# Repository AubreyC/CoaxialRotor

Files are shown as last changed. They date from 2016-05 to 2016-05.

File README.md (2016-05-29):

Coaxial-Rotor instructions
==========================

This document presents the main steps to build a flyable coaxial-rotor UAV. 

## Manufactering process
	
The Coaxial-rotor UAV is composed of off-the-shelf electronic parts and plywood / foam-board laser cut parts. The following list of components and CAD files corresponds to a medium-size configuration shown in the following picture. 

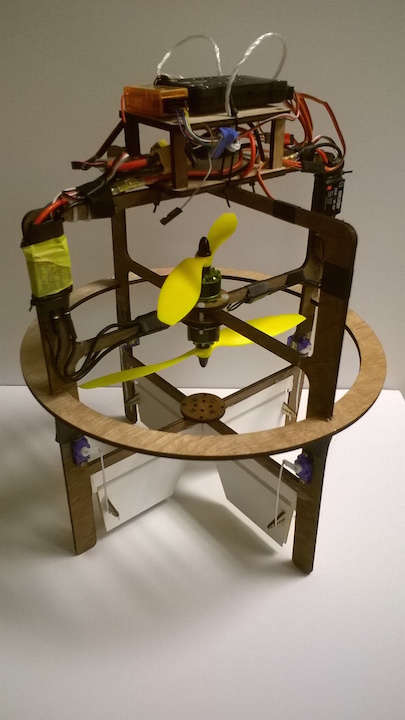
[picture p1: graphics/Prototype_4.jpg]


Assembled Prototype

### Off the shelf

- PIXHAWK Hardware Autopilot 
- RC receiver: OrangeRx R615X
- Battery : XXX
- ESC (with BEC): 2 x Mystery 30A M-30 with BEC 5V
- Motors: 2 x Multistar 2209-1200 
- Propellers: 2 x 
- 4 servomotors: 4 x Hextronik HXT 500

### Manufactering:
##### Material needed  
- Plywood (6mmm and 3mm)
- Foam-board (6mm)
- Laser-cut machine 
- Hot glue 
- Zip-ties

##### CAD files

This Coaxial-rotor UAV has been designed to be fully laser-cut, and assembled using hot-glue and zip-ties. The CAD files are in the [CAD folder](https://github.com/AubreyC/CoaxialRotor/tree/master/CAD). 

###### Plywood 5mm:
- Main Frame: Part 1 (frame_1.SLDPRT) / Part 2 (frame_2.SLDPRT)
- Motor mount: 2 x Part (motorMount.SLDPRT)
- Autopilot Plate: 2 x Part (plate.SLDPRT)
- Column plate: 4 x (columnPlate_long.SLDPRT / columnPlate_short.SLDPRT)

###### Plywood 2.5mm:

- Hinge: 4 x Part (hinge.SLDPRT)

######  Foam-board (6mm):
- Control surfaces: Part 1 (controlSurface_1_v2.SLDPRT) / Part 2 (controlSurface_2_v2.SLDPRT) 
	
__NOTE:__ On the control surface, the second line needs to be scored (and not cut), in order to create a hinge with the foam-board.

##### Laser-cut settings (Epilog Legend 36 EXT)

| Foam-board | Speed | Power  | Frequency |
| --- |:---:| :----: |:---:|
| Scoring | 90		 | 100 | 5000		 |		
| Cutting | 40 	 | 100 | 5000		 |

| Plywood 	| Speed | Power  | Frequency |
| ---|:---:| :----: |:---:|
| Cutting (3mm) | 25		 | 	100  | 500	 |		
| Cutting (6mm) | 8  	 | 100  | 500 	 |

## Code base:

For the flight control, the [PX4 flight stack](http://px4.io/) is used for its modularity and clarity as flight control software. 

The devlopment is done under linux [Ubuntu 14.04 LTS](http://releases.ubuntu.com/14.04/). The easiest way to get started is to build a virtual machine using [VirtualBox](https://help.ubuntu.com/community/VirtualBox). 

The PX4 development toolchain needs to be installed. Please follow the instructions: [PX4 flight stack - Installing toolchain](http://dev.px4.io/starting-installing-linux.html).

A lots of additional information can be found in the [PX4 flight stack - Development Guide](http://dev.px4.io). 

### Coaxial-rotor controller

Using the PX4 flight stack allows to re-use most of the code base, and to adapt it for this configuration. 

The coaxial-rotor uses the same controller as a quadcopter, and re-map the output of the controller (forces and torques to apply to the system) to the actuators. The mapping from the output of the attitude controller to the actuators is called the [PX4 flight stack - Mixer](http://dev.px4.io/concept-mixing.html).

For the Coaxial-rotor design, the mixer is designed as shown in the following figure: 

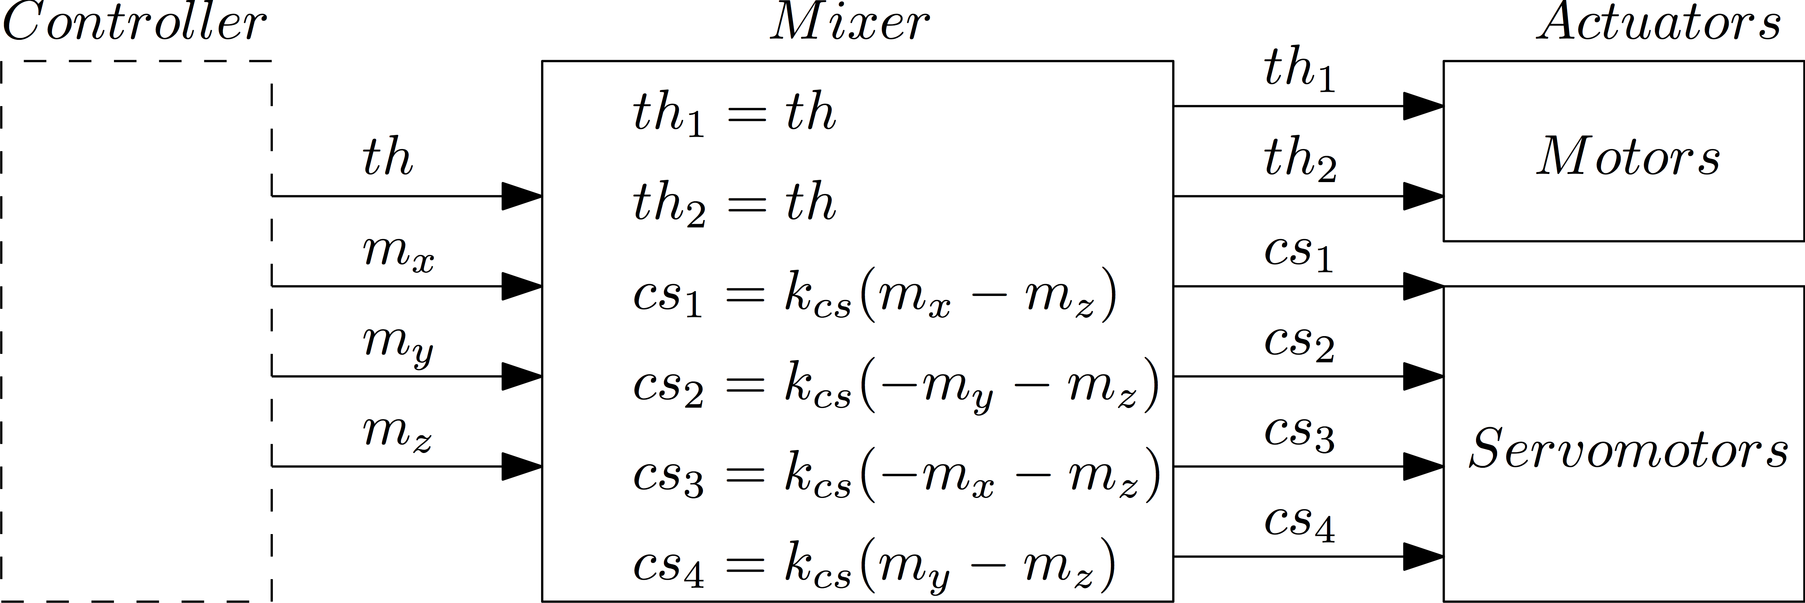
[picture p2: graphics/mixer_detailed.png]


#### Modifications
 
To support this configuration, the following modifications have been made to the base code: 
- __New Start up script__: Start the appropriate modules for this configuration [Start up - Coaxial-rotor](https://github.com/AubreyC/Firmware/blob/coaxial_rotor/ROMFS/px4fmu_common/init.d/15002_coax_rotor)
- __New Mixer__: Map the output of the attitude controller to the actuators. [Mixer - Coaxial-rotor](https://github.com/AubreyC/Firmware/blob/coaxial_rotor/ROMFS/px4fmu_common/mixers/coax_rotor.main.mix)
- __Low pass filter__: Applied on the outputs of the controller / inputs of the mixer (aka forces and torques to apply on the system) [Mixer - Coaxial-rotor](https://github.com/AubreyC/Firmware/blob/coaxial_rotor/src/modules/mc_att_control/mc_att_control_main.cpp)
- __Different attitude gains__: The gains are defined as parameters in the "Attitude Control" section of the parameter list. 

The changes have been incorported in the following version of the PX4 codebase (as a git fork) [PX4 flight stack - Coaxial-rotor version](https://github.com/AubreyC/Firmware/tree/coaxial_rotor) (make sure to select the "coaxial_rotor" branch). 

Clone the git to get a local copy of the code:

	git clone https://github.com/AubreyC/Firmware.git

https://github.com/PX4/Firmware

__NOTE:__ It is possible to start from the official [PX4 flight stack - Github](https://github.com/PX4/Firmware) and to make the modifications manually. In order to do that add: 
- [Start up - Coaxial-rotor](https://github.com/AubreyC/Firmware/blob/coaxial_rotor/ROMFS/px4fmu_common/init.d/15002_coax_rotor) to *Firmware/ROMFS/px4fmu_common/mixers*
- [Mixer - Coaxial-rotor](https://github.com/AubreyC/Firmware/blob/coaxial_rotor/ROMFS/px4fmu_common/mixers/coax_rotor.main.mix) to *Firmware/ROMFS/px4fmu_common/init.d*
- Add the low-pass filter to the Attitude Controller outputs: *Firmware/blob/coaxial_rotor/src/modules/mc_att_control/mc_att_control_main.cpp*

#### Building and configuring

Follow the instructions from the [PX4 flight stack - Building the code](http://dev.px4.io/starting-building.html).

Open a console and navigate to the *Firmware* folder of the code.

Building: 

	make px4fmu-v2_default

Building and uploading: 

	make px4fmu-v2_default upload

Once the code is uploaded on the PIXHAWK, some parameters need to be changed for the coaxial-configuration: 
- SYS_AUTOSTART: set it to __15002__ which corresponds to the custom start-up script.
- Attitude Gains: Gains are proposed as a start but are probably not optimal. It is recommended to tune them for better performances. 

###### Proposed Gains: 
	MC_ACRO_P_MAX	360.0
	MC_ACRO_R_MAX	360.0
	MC_ACRO_Y_MAX	360.0
	MC_PITCHRATE_D	0.0015
	MC_PITCHRATE_FF	0.0000
	MC_PITCHRATE_I	0.03
	MC_PITCHRATE_MAX 220.0
	MC_PITCHRATE_P	0.075
	MC_PITCH_P	3.25
	MC_PITCH_TC	0.16
	MC_RATT_TH	1.00
	MC_ROLLRATE_D	0.0015
	MC_ROLLRATE_FF	0.0000
	MC_ROLLRATE_I	0.025
	MC_ROLLRATE_MAX	220.0
	MC_ROLLRATE_P	0.075
	MC_ROLL_P	3.25
	MC_ROLL_TC	0.16
	MC_YAWRATE_D	0.00
	MC_YAWRATE_FF	0.0000
	MC_YAWRATE_I	0.00
	MC_YAWRATE_MAX	200.0
	MC_YAWRATE_P	0.10
	MC_YAWRAUTO_MAX	45.0
	MC_YAW_FF	0.50
	MC_YAW_P	1.40

__NOTE:__ The [Parameter file](https://github.com/AubreyC/CoaxialRotor/blob/master/parameters/parameters_PX4_CoaxialRotor.params), from one flying prototype has been saved. This file contains the attitude gains, as well as the system start-up number for the coaxial-rotor configuration. Be carefull, this parameter file also contains all the calibration data, which are different from one system to the other.

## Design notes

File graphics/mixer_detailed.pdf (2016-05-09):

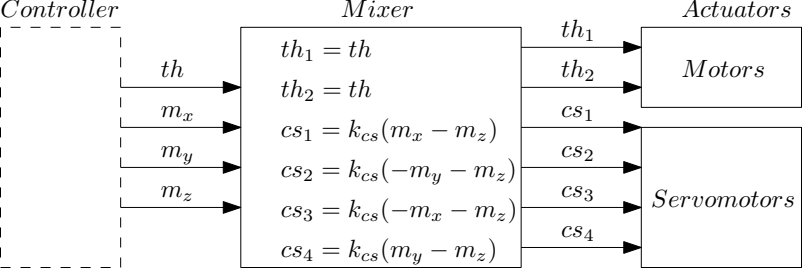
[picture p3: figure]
Controller; cs1 = kcs(mx − mz); cs2 = kcs(−my − mz); cs3 = kcs(−mx − mz); cs4 = kcs(my − mz); M ixer; Servomotors; Motors; Actuators

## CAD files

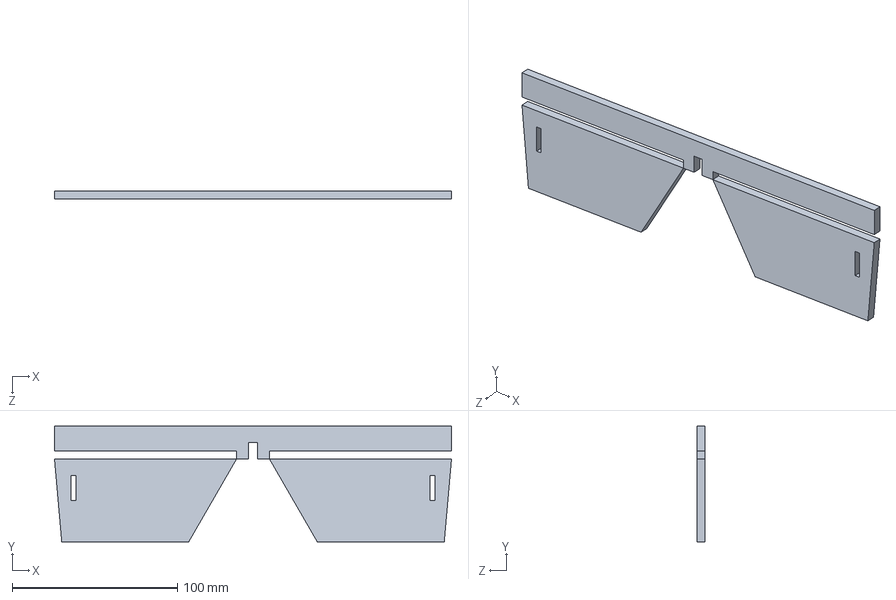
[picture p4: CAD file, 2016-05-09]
CAD/controlSurface_1.SLDPRT
240.0 x 70.0 x 5.00 mm

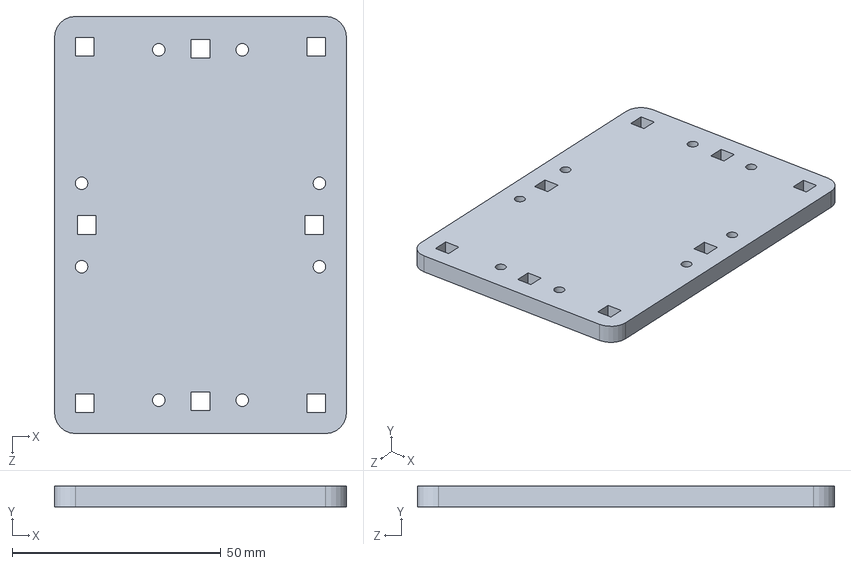
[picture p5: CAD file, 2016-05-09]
CAD/plate.SLDPRT
70.0 x 5.00 x 100.0 mm

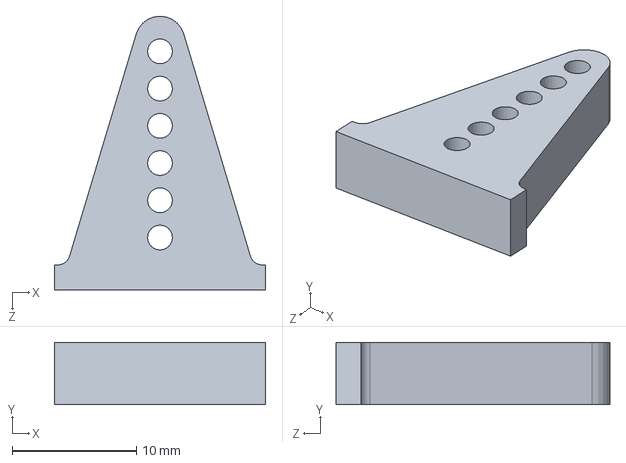
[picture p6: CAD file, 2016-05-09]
CAD/horn.SLDPRT
17.0 x 5.00 x 22.0 mm

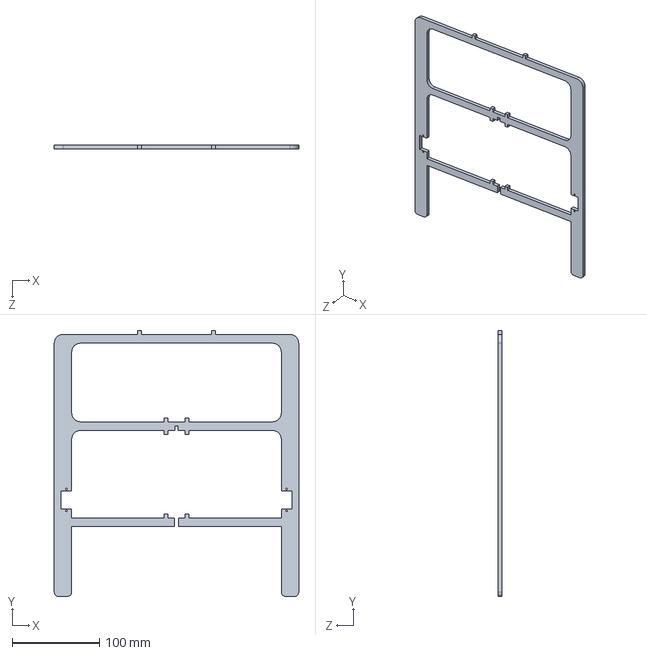
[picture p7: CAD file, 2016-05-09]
CAD/frame_1.SLDPRT
280.0 x 304.5 x 5.00 mm

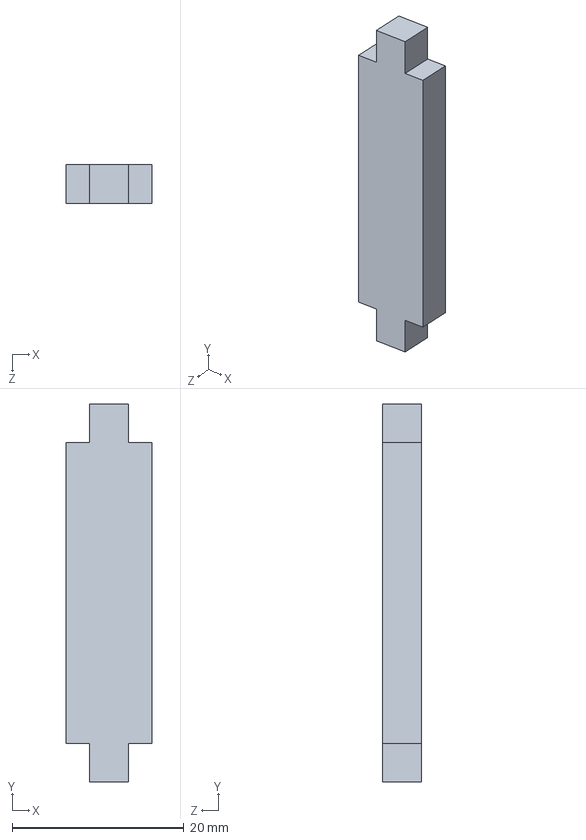
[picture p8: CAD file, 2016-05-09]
CAD/columnPlate_long.SLDPRT
10.0 x 44.0 x 4.50 mm

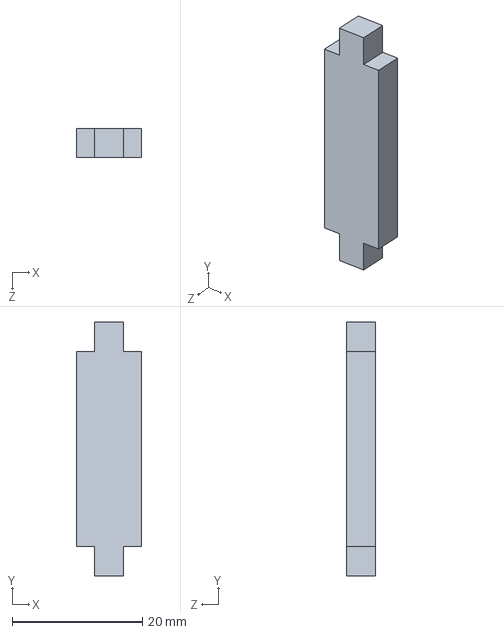
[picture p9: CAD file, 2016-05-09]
CAD/columnPlate_short.SLDPRT
10.0 x 39.0 x 4.50 mm

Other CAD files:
CAD/printer/Print_full_V1.DWG
CAD/extra_parts/Stiffness_servo.SLDPRT
CAD/printer/Horns_Print.DWG
CAD/extra_parts/Stiffness.SLDPRT
CAD/printer/controlSurface_Print.DWG
CAD/controlSurface_2.SLDPRT
CAD/printer/face1.DWG
CAD/printer/motorMount_print.DWG
CAD/printer/Horns.DWG
CAD/printer/Horns_print_v2.DWG
CAD/frame_2.SLDPRT
CAD/printer/print_v1.DWG
CAD/controlSurface_1_v2.SLDPRT
CAD/controlSurface_2_v2.SLDPRT
CAD/hinge.SLDPRT
CAD/motorMount.SLDPRT
CAD/protection_ring.SLDPRT

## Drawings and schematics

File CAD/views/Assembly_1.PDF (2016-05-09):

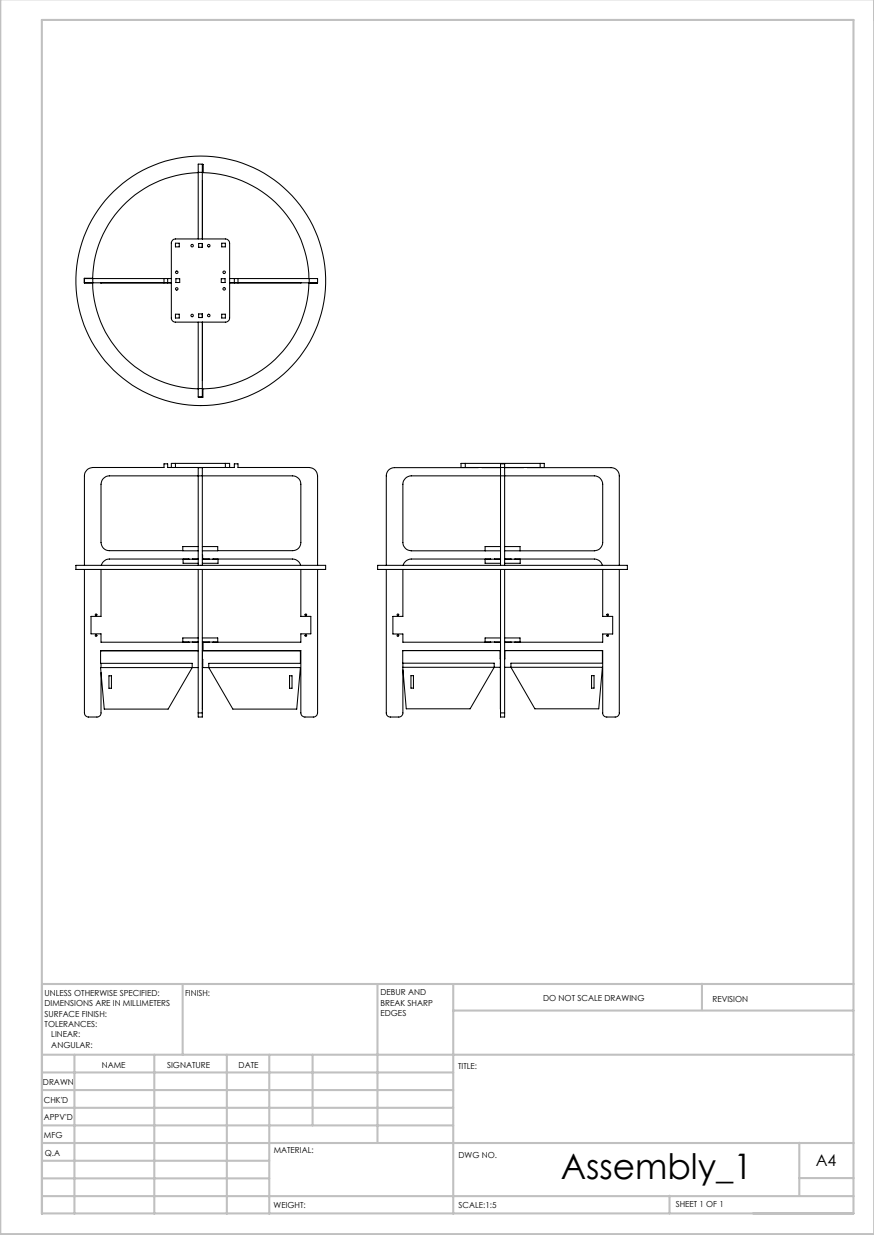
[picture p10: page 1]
SCALE:1:5; SHEET 1 OF 1; DO NOT SCALE DRAWING; REVISION; DEBUR AND BREAK SHARP; UNLESS OTHERWISE SPECIFIED:; FINISH:

DIMENSIONS ARE IN MILLIMETERS
SURFACE FINISH:
TOLERANCES:
LINEAR:
ANGULAR:

NAME | SIGNATURE | DATE | | | | TITLE:
Q.A | | | | MATERIAL: | Assembly_1 WEIGHT: DWG NO. | A4

DRAWN
CHK'D
APPV'D
MFG

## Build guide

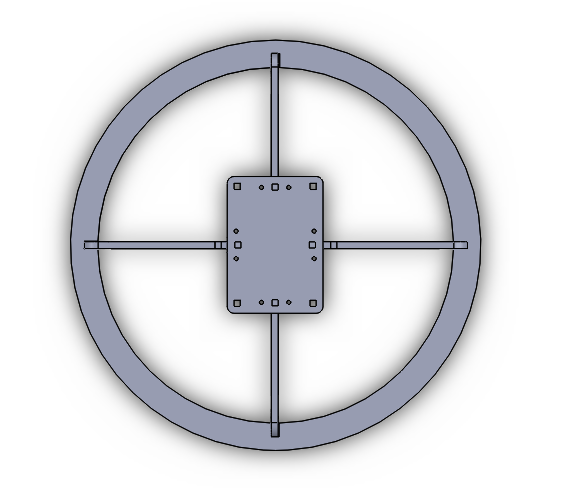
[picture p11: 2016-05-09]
CAD/views/assembly_top.PNG

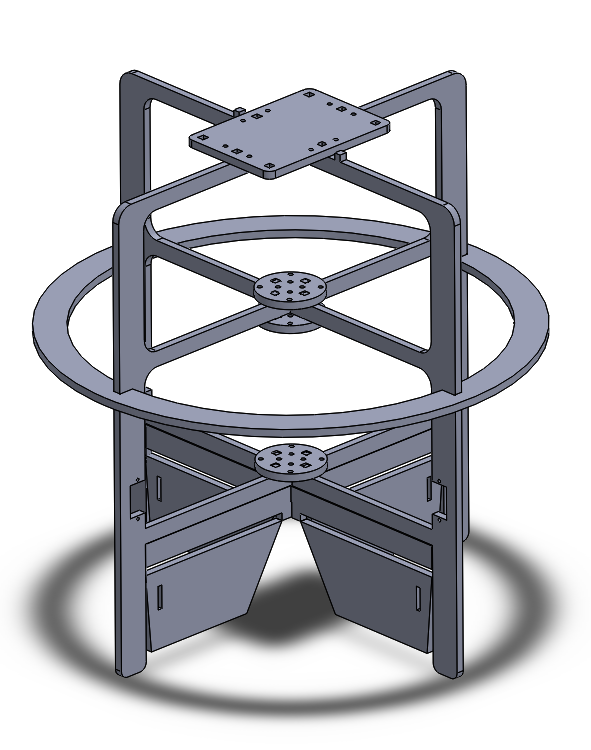
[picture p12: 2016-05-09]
CAD/views/assembly_full.PNG

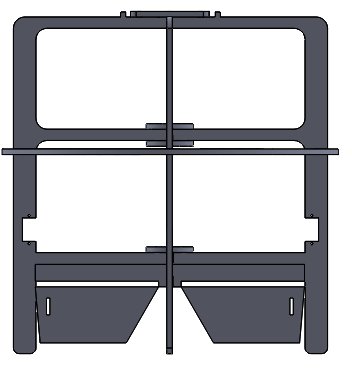
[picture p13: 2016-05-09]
CAD/views/assembly_profil_1.PNG

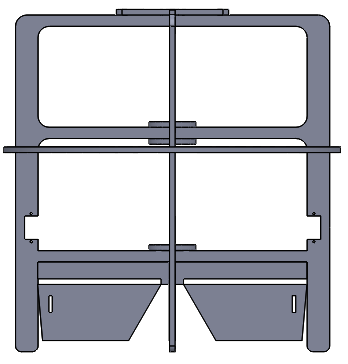
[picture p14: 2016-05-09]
CAD/views/assembly_profil_2.PNG

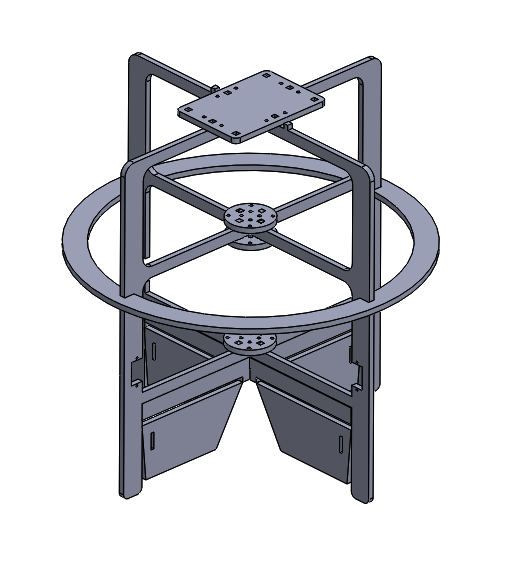
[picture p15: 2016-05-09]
CAD/views/assembly_full_no_shadow.PNG

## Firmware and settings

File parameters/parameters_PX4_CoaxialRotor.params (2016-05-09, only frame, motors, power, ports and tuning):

1	1	BAT_CAPACITY	-1	9
1	1	BAT_C_OFFSET	-1.000	9
1	1	BAT_C_SCALING	-1.000	9
1	1	BAT_N_CELLS	3	6
1	1	BAT_V_CHARGED	4.20	9
1	1	BAT_V_EMPTY	3.40	9
1	1	BAT_V_LOAD_DROP	0.07	9
1	1	BAT_V_SCALE_IO	10000	6
1	1	BAT_V_SCALING	-1.000	9
1	1	MC_PITCHRATE_D	0.0015	9
1	1	MC_PITCHRATE_FF	0.0000	9
1	1	MC_PITCHRATE_I	0.03	9
1	1	MC_PITCHRATE_MAX	220.0	9
1	1	MC_PITCHRATE_P	0.075	9
1	1	MC_PITCH_P	3.25	9
1	1	MC_PITCH_TC	0.16	9
1	1	MC_ROLLRATE_D	0.0015	9
1	1	MC_ROLLRATE_FF	0.0000	9
1	1	MC_ROLLRATE_I	0.025	9
1	1	MC_ROLLRATE_MAX	220.0	9
1	1	MC_ROLLRATE_P	0.075	9
1	1	MC_ROLL_P	3.25	9
1	1	MC_ROLL_TC	0.16	9
1	1	MC_YAWRATE_D	0.00	9
1	1	MC_YAWRATE_FF	0.0000	9
1	1	MC_YAWRATE_I	0.00	9
1	1	MC_YAWRATE_MAX	200.0	9
1	1	MC_YAWRATE_P	0.10	9
1	1	MC_YAWRAUTO_MAX	45.0	9
1	1	MC_YAW_FF	0.50	9
1	1	MC_YAW_P	1.40	9
1	1	PWM_MAIN_REV1	0	6
1	1	PWM_MAIN_REV2	0	6
1	1	PWM_MAIN_REV3	0	6
1	1	PWM_MAIN_REV4	0	6
1	1	PWM_MAIN_REV5	0	6
1	1	PWM_MAIN_REV6	0	6
1	1	PWM_MAIN_REV7	0	6
1	1	PWM_MAIN_REV8	0	6
1	1	SYS_AUTOSTART	15002	6

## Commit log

2016-05-09 CAD files
    [Horns.DWG, Horns_Print.DWG, Horns_print_v2.DWG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]
2016-05-09 readMe cad folder
